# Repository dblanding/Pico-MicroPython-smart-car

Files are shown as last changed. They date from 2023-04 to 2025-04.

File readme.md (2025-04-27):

# Pico-&mu;Python Smart Car Project

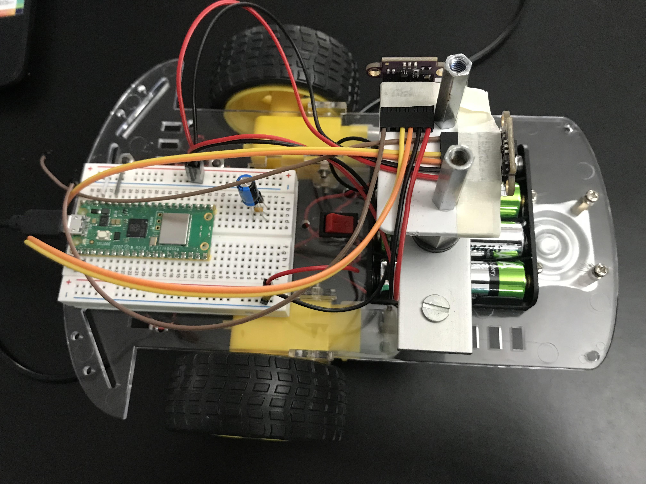
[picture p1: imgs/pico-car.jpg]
pico car


### This Medium article by Dan McCreary [Raspberry Pi Pico Robot in Micropython](https://dmccreary.medium.com/raspberry-pi-pico-robot-in-micropython-51f956486270) inspired me to buiild a similar smart car project
* Further details are presented at [base robot kit project](https://dmccreary.github.io/stem-robots/)
    * Discovered they use [MkDocs](https://www.mkdocs.org/getting-started/). May want to check this out sometime...

### My project will use **at least 2** of these time-of-flight VCSEL sensors

* Googled for info about Using the Raspberry Pi Pico with 2 x VL53L0x in Micropython
    * Found this [Orionrobots video](https://www.youtube.com/watch?v=XQrxPcq2tZ8) which shows:
        * Using two devices, one on each I2C bus
        * How to modify device address in order to have multiple devices on the same bus
        * in both cases, it is important to hold the XSHUT pin high.
    * The library used by Orionrobots is based on Kevin McAleer's [Raspberry Pi Pico & VL53L0X for MicroPython](https://www.youtube.com/watch?v=YBu6GKnN4lk)
    * Unfortunately, The library used (by both Kevin McAleeer and the derivative Orionrobots) only produces values up to 500 mm.
        * Whereas the datasheet shows the VL53L0X should produce data up to 1200 mm.
        * The VL53L0X library (used by McCreary) produces values all the way to 1200 mm. 
            * A diff shows that the libraries used by McAleer (and Orionrobots) is actually a mofified version of the one used by McCreary.
* I thought I would try using the **disparity** of two forward-looking but obliquely oriented (pigeon-toed) sensors as a way to enable the cheap *smart-car* to steer toward a wall along a path that is perpendicular to the wall. This proved to be quite difficult.
    * Without motor encoders, it is very frustrating trying to control steering on differential drive configuration.
    * The motors have a large and varialble amount of static friction, causing the actual motor speed to be unknowable. 
    * Sometimes, the friction is so large, that a motor won't start to turn even with a PWM duty cycle of (40_000 / 65_536)
    * Decided to not pursue this approach any further.
* Instead, I decided to use the Bosch BNO08x IMU sensor in RVC mode to keep track of the car's yaw angle.
* I will use the VCSEL sensors just for distance measurement

### Use the Bosch BNO08x IMU sensor to keep track of the car's **yaw** angle

* I found this [MicroPython library](https://github.com/rdagger/micropython-bno08x-rvc/blob/master/bno08x_rvc.py) (based on this [CircuitPython library](https://github.com/adafruit/Adafruit_CircuitPython_BNO08x_RVC)) which enables access to the BNO08x IMU module (in RVC mode) over the UART serial bus.
* (Truth be known, I was having a bit of difficulty figuring out how to attach more than one device to the I2C bus, so I decided to just sidestep this issue and connect over UART.)
* This primer on [Raspberry Pi Pico Serial Communication Example(MicroPython)](https://electrocredible.com/raspberry-pi-pico-serial-uart-micropython/) provided the detailed understanding I needed to get it all working.

### Use the [L298N motor driver module](https://www.etechnophiles.com/l298n-motor-driver-pin-diagram/)
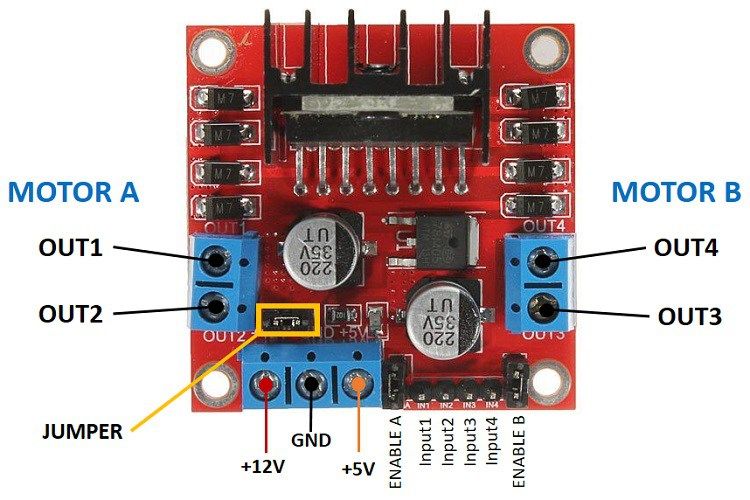
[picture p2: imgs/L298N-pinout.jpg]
L298N pinout

* Used on my ROS robot and it worked well, so I will use that again.

### Power to the pico will come from 2 different sources:
    1. The USB connection (5V)
    2. The 5V power output from the motor driver board
    
* The Pico datasheet shows a recommended way to accomodate power from 2 sources:

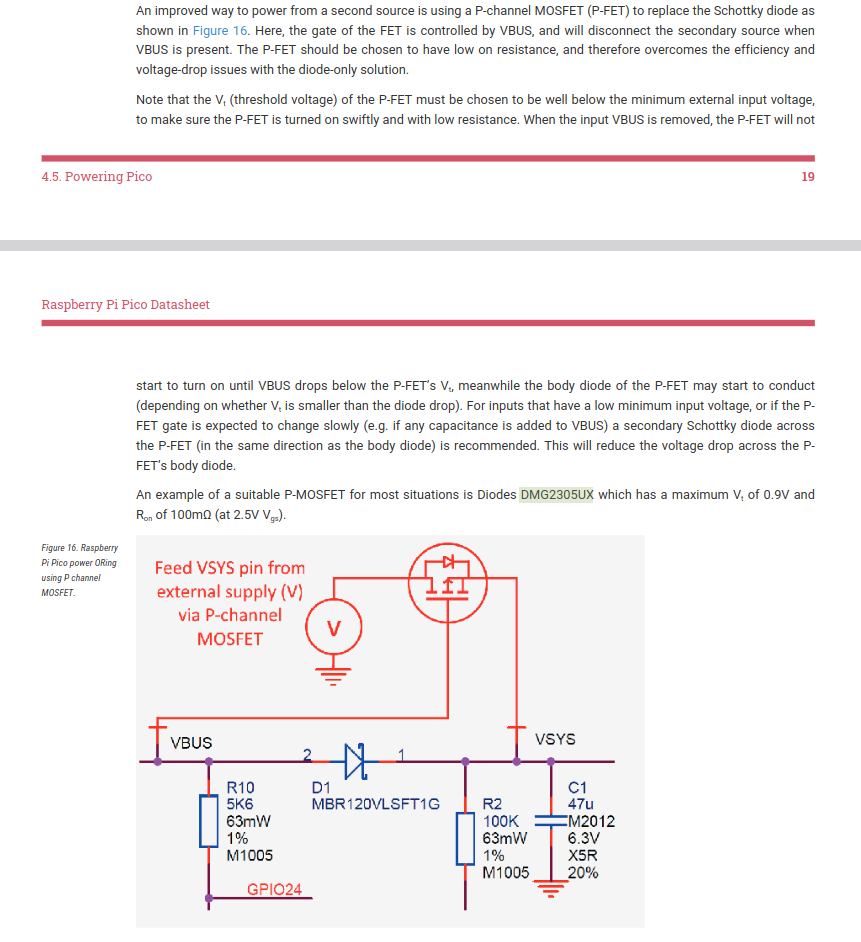
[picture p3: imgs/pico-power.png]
pico power


* I ordered the P-FET but until it comes, I have hooked up the 5V output from the motor driver board directly to the VSYS pin of the pico, as shown in this wiring diagram. It seems to work OK both with / without the USB connection to the Pico.

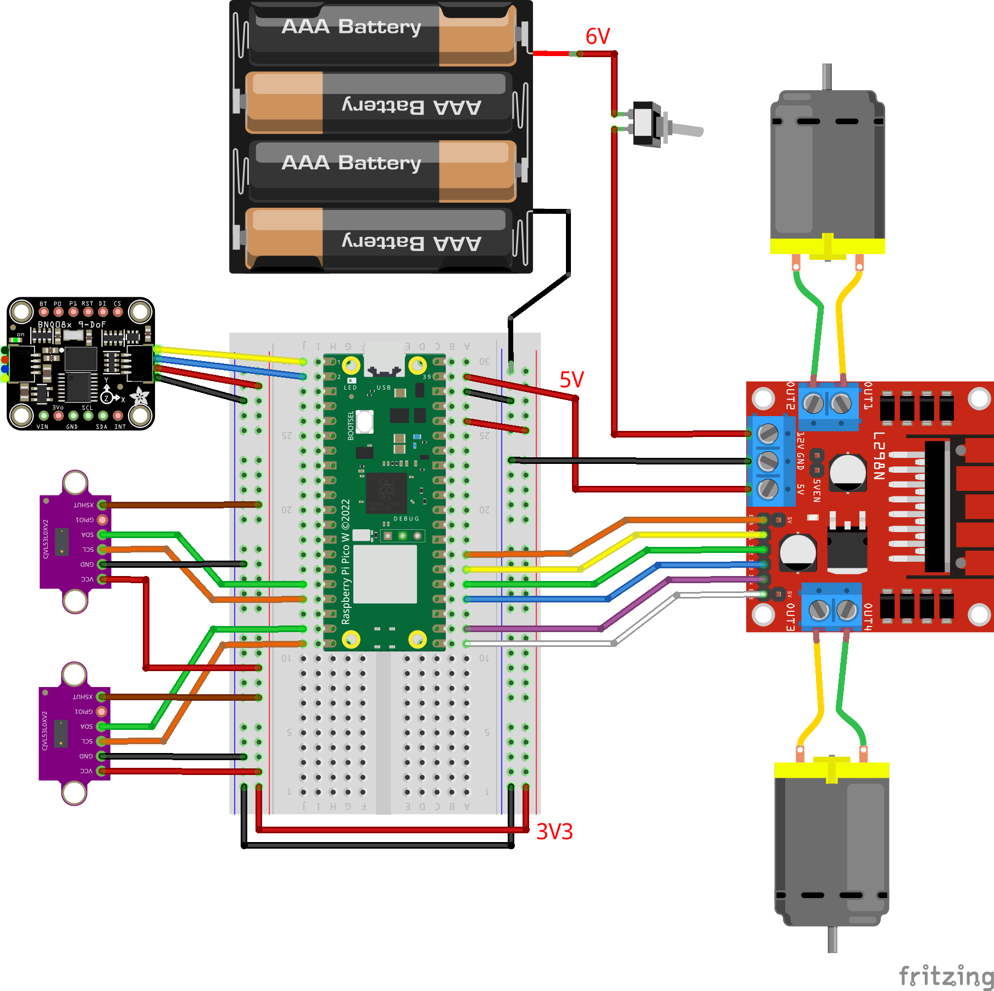
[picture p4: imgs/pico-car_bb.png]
Pico car wiring


* This video [Power for the Raspberry Pi Pico - Guide to using VBUS, VSYS and 3V3 for external power circuits](https://www.youtube.com/watch?v=3PH9jzRsb5E) reccomends using a Schotkey diode (1N5817) to allow connecting an external 5V supply to VSYS while the PICO is simultaneously connected to USB power.

### Add WiFi control

Bob Grant ([Bytes N Bits](https://bytesnbits.co.uk/S)) has produced this series of [3 video tutorials](https://www.youtube.com/playlist?list=PLvOT6zBnJyYGLmvrJeYzRYwBFa44SVnLZ) which teach how to build a web interface for controlling a project on the Pi Pico W.
* WiFi Control Your Micropython Project Using a Web Interface
    * [Youtube video](https://www.youtube.com/watch?v=eym8NpHr9Xw)
    * [Bytes N Bits web page](https://bytesnbits.co.uk/simple-micropython-wifi-connection/)
    * [Github Repo](https://github.com/getis/pi-pico-w-simple-wifi-setup)

* Web Control Panel Part 1: Add a web control panel to your project - the web server
    * [Youtube video](https://www.youtube.com/watch?v=h18LMskRNMA)
    * [Bytes N Bits web page](https://bytesnbits.co.uk/web-control-panel-web-server/)
    * [Github Repo](https://github.com/getis/micropython-web-control-panel)

* Web Control Panel Part 2: Asyncio & Dual Core web server
    * [Youtube video](https://www.youtube.com/watch?v=PY732g2ZN4g)
    * [Bytes N Bits web page](https://bytesnbits.co.uk/web-control-panel-2-asyncio-dual-core/)
    * [Github Repo](https://github.com/getis/micropython-web-control-panel)

* Web Control Panel Part 3: Web Page & Javascript coding
    * [Youtube video](https://www.youtube.com/watch?v=Z6g9x170Pvw)
    * [Bytes N Bits web page](https://bytesnbits.co.uk/web-control-panel-web-page/)
    * [Github Repo](https://github.com/getis/micropython-web-control-panel)

But first, just to get started, I will use a more primitive, basic web control interface.
Christopher Barnatt shows a very simple [Pi Pico W WiFi Controlled Robot](https://www.explainingcomputers.com/pi_pico_w_robot.html)
* The robot runs a basic webserver displaying a very simple form with 5 buttons.

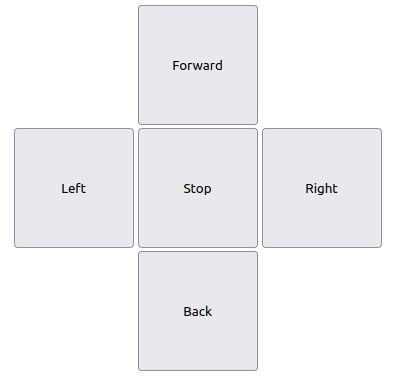
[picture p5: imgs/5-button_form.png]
webpage form


This looks just right for this project. Simple and straightforward. I just need the webserver to run asynchronously so it doesn't block the robot's navigation code.
* `pico_car+webserver.py` combines the web interface code the navigation code bundled together.

## Pause for project assessment

At this point, I have a nice, cheap mobile car platform for testing various robot-related concepts. And it is all running on the PICO-W.

Right now, if I set the car on the floor and turn it on, and then go to my laptop and browse to the car's webserver url (192.168.1.64), I get the car's 5-button navigtation panel.
* If I click the **Back** button, the car drives in reverse and it uses the PID feedback from the IMU to drive roughly straight in reverse (with some minor steering oscillations) until it arrives to within  250 mm of a wall.
* However if I click on the **Forward** button, the car goes forward, but drives as if it had a *steering wheel* that was turned 90 degrees to the left.
    * The left wheel was runnning slower than the right one.
    * Probably due to friction (I thought)
    * One possible cause was that the face of the left wheel hub was rubbing more against the motor housing, so I pried the wheel hubs away from the motor housing to create a small gap, but the problem persisted.
    * Whatever the cause of the difference in performance between the left and right motors, it is pointless to chase it down. There will always be differences.
    * Using yaw angle feedback from the IMU, I can get the car to drive straight in both the forward and reverse directions, but when turning in place, I won't know that both motors are turning (at the same speed).
        * For this reason, I decided that the motors must have encoders and the PID feedback from the encoders must be used to regulate the motor drive signals.
        * This of course, is the configuration of the ROS mobile robot, which makes further use of the encoder information to accurately compute odometry.

* Having come to the following realization, I decided to scrap the original chassis and motors, and begin again from scratch:

> The cute little yellow motors that come on the **DIY Smart Car** are altogether **inadequate** for use on a DIY robot. Any serious robot project must have motor shaft encoders and a gearbox with a reduction of at least 30 to 40x.

# Henceforth, this project is renamed **PicoBot**

* The original code is in the folder `code_other/`.
* The PicoBot code is in the folder `code_picobot/`.

## Find inexpensive gear motors with encoders for the Pico Car

I have been down this road previously and the best motors/wheels I found were the ones used by the Elegoo Tumbller. For the ROS robot, I wanted a higher gear reduction and ended up using motors with a 100:1 worm drive gear box.

For this project, I am not convinced that I need a different gear reduction, so I will proceed with the motors/wheels used by the Tumbller. I found them available for $12 apiece on [Aliexpress](https://www.aliexpress.us/item/2251832832394397.html?gatewayAdapt=glo2usa4itemAdapt) and [ordered 2](aliexpress-order/aliexpress-order.pdf).  There is a chart that shows various gearabox options. The Tumbller motor has a 30:1 gearbox with a length of 22 mm. Higher gear reductions can be gotten but have a greater length.  When I was looking for higher reduction motors for the ROS robot, I hadn't found these motors from Aliexpress. Looking at the Tumbller, it looks like there is enough room for the 24 mm length gearbox. So I could choose either 56:1 or 90:1 gear reductions.

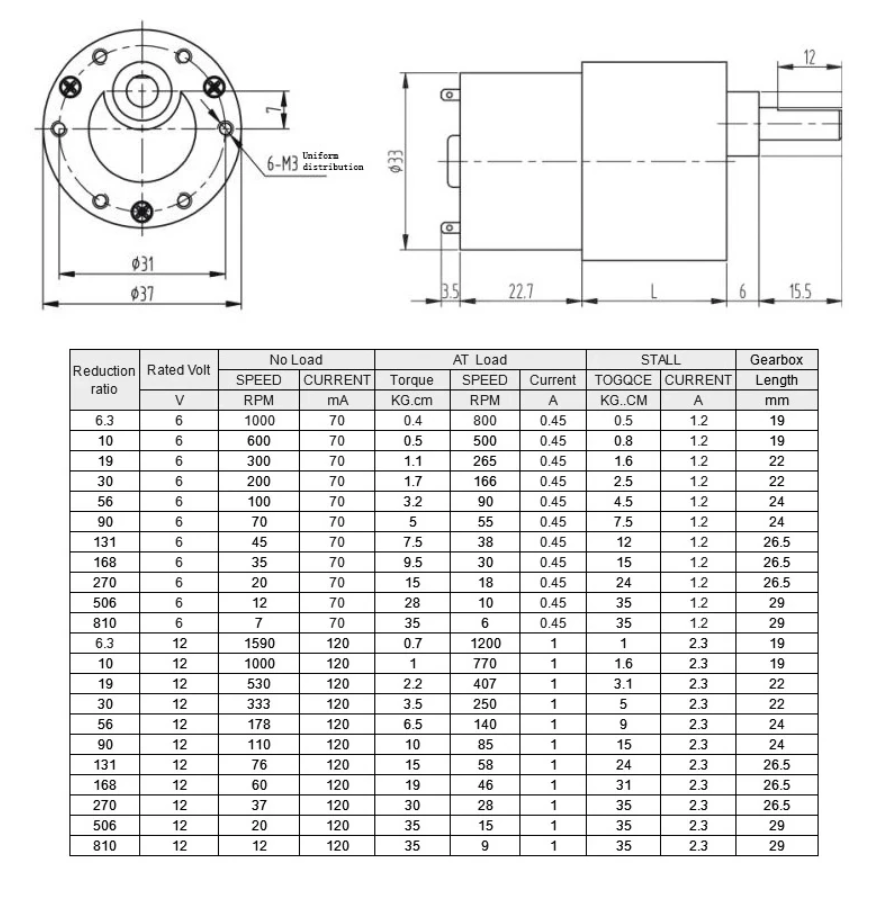
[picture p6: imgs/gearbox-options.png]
Gearbox Options


The motors come with a 6-wire harness which needs to be hooked up as follows:

- Red Wire - positive power supply of motor(+)(change positive and negative of motor the rotation will change)
- White Wire - negative power supply of motor(-)(change positive and negative of motor the rotation will change))
- Yellow Wire - signal feedback (motor one turn has 11 signals)
- Green Wire - signal feedback (motor one turn has 11 signals)
- Blue Wire - positive of encoder power supply(+)(3.3-5V),cannot be wrong
- Black Wire - negative of encoder power supply(-)(3.3-5V),cannot be wrong

## Program PICO to listen to encoder pulses on interrupts

Using the method shown in this video [Using PICO interrupts](https://www.youtube.com/watch?v=9Fio0BlMsVM), Chris DeHut shows how to set up the PICO to listen to encoder pulses.

* In the video, he has a link to the [code](https://makingstuffwithchrisdehut.com/electronics-files) which looks like an absolute gold mine of useful code for the PICO.

* For example, there are files there named: "encoders" and "analog joystick".
Those look like they would be worth looking at...

I found a collection of [Awesome MicroPython](https://awesome-micropython.com/#rotary-encoder) libraries which contains an encoder primer by Peter Hinch at this [repo](https://github.com/peterhinch/micropython-samples/blob/master/encoders/ENCODERS.md)
* He has written an [encoder library specifically for the Pico](https://github.com/peterhinch/micropython-samples/blob/master/encoders/encoder_rp2.py)
    * It uses some PIO and State Machine code (over my head) but seems to work very well, so I decided to use it. 
        * It counts **52 pulses per rev** which is likely counting both rising and falling edges of both sensors. (13 poles x 4)
        * This differs from the *"11 signals per rev"* quoted by the spec sheet (above).

## Pause again to evaluate project progress

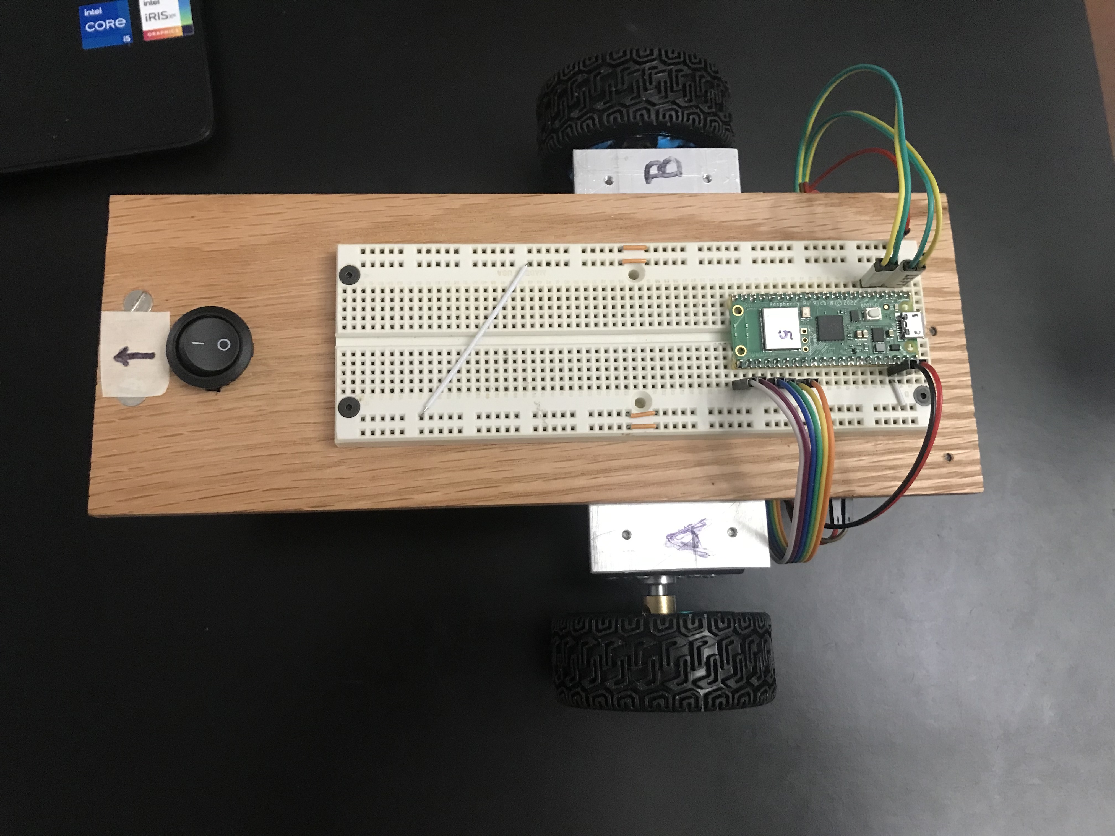
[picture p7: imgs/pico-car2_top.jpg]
Pico Car 2 (top)

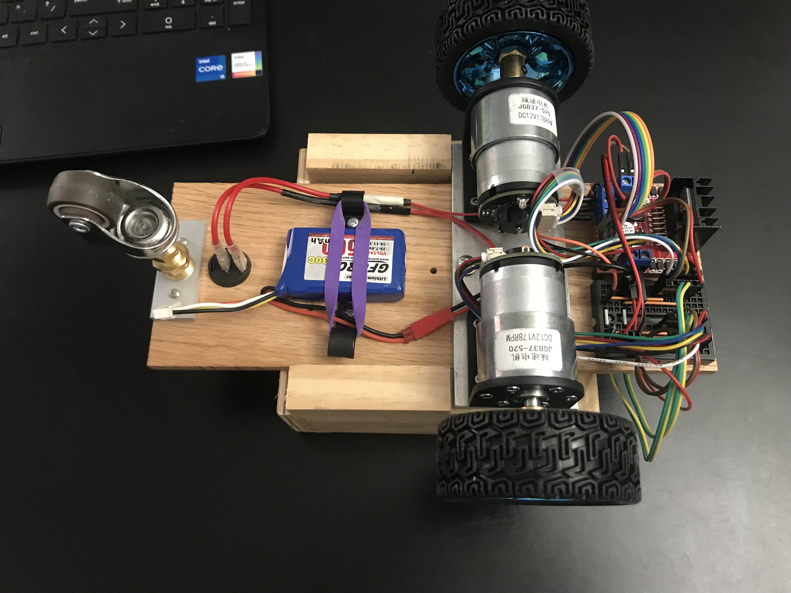
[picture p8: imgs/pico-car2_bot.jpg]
Pico Car 2 (bot)


* The car has been completely rebuilt to replace the little yellow smart car motors with the Tumbller motors. However, the new motors still have intrinsic differences that cause the car to turn excessively when intending to drive straight with the application of equal PWM signals.
* I replaced the 4-pack of AA batteries with a LiPo 3S 50C battery. This was to remedy the problem that as the AA batteries got a little tired, the 5V PS on the L298N was unable to provide 5V out and therefore was unable to power the Pico.
    * This solved the problem with the L293N P/S, but now the motors run much **faster** than they need to, so in order to operate at a moderate speed, a lower PWM signal is needed.

* I have received and installed the motors I ordered from AliExpress. (3 weeks from order to arrival)
    * It turns out they are the 56:1 motors.
    * This gear reduction works very well.
        * The cruising speed of the car is fine with the LiPo battery 
        * In-place turning works great with lower PWM values.
        * Decided to order another pair (spares)
    * For now, I drive the motors at a target tick rate of 4000 ticks/sec by applying an individual multiplier for each motor to arrive at a PWM signal that runs them both at approximately the same speed.
        * The PWM signals are in the vicinity of 50_000 (max value = 65,535)

* I am still using the 5-button web interface (asynchrouous) to control the car. This works OK, but it is pretty bare bones. I might want to explore a joystick for speed and direction control.
* I removed the VCSEL sensors and the IMU (for now) while I focus on getting the motors to use PID feedback from the encoders to drive at a target tick rate.

## Implement closed loop feedback motor speed control

* Wheel diameter = 2.682 inches (68.12 mm)
* Use encoder pulses in proportional feedback loop to control speed while driving forward and backward
* Using `encoder_test.py`, I found 2464 ticks for each revolution of the wheel.

| Factor | Source |
| ---- | ---- |
| 56 x | gear reduction |
| 11 x | magnetic poles on rotor |
|  4 x | detecting both rising and falling edges from 2 (quadrature) sensors |
| 2464 | Total (ticks per wheel rev) |

| Value | Parameter |
| ---- | ---- |
| 0.214 | Wheel circumference (meters) |
| 11_514 | ticks per meter |

* Even after optimizinging PID coefficients, there is still some visually detectable *wiggle* in the car's steering as it begins driving straight forward or backward.
    * Small differences in friction between the 2 motors cause them to come up to speed differently even under the control of the feedback loop.
    * To reduce this steering wiggle, I will try adding a 4th term (C) to the controller, minimizing the difference between the encoder counts of the two motors.
    * Adding a 'C' term makes the PID controller into a PIDC controller.
    * The C term keeps track of the cumulative tick counts for both motors, urging them to stay in lock step.
* To implement this, a single instance of the new motors.Motors class replaces the 2 instances of motor.Motor class. 
    * P (proportional)
    * I (integral)
    * D (Derivative)
    * C (count difference a / b)
* Got this working in both Forward & Back directions.
    * The steering wiggle is no longer visually noticeable.
    * Performance data of some 1 meter runs (FWD & BACK) are shown in [spreadsheets folder](spreadsheets).

## Other refinements

* Added Odometer class, which updates pose each time through the main loop.
    * `pose = Odometer.update(enc_a.value(), enc_b.value())`
    * `pose_x, pose_y, pose_angle = pose`
* Using pose_angle, left and right buttons can now turn to a goal_angle.
* Using encoder_values, driving forward and back can go to a goal_distance.

## Implemented Programmed Driving Instructions

* The main loop now loads the `instrux` list containing a sequence of `(drive_mode, goal)` tuples and executes them one-by-one.
* For example, here are the instructions to drive a 0.5 meter square in the CCW direction:
```
instrux = [('F', 0.5),
           ('L', pi / 2),
           ('F', 0.5),
           ('L', pi),
           ('F', 0.5),
           ('L', 3 * pi / 2),
           ('F', 0.5),
           ('L', 2 * pi)]
```

* After completing the sequence, the PicoBot continues to respond to web requests.

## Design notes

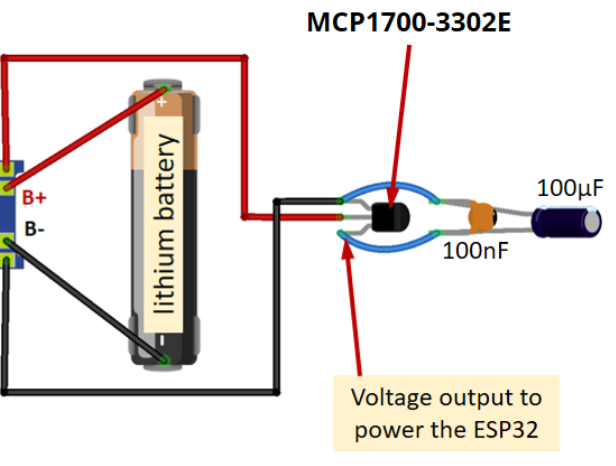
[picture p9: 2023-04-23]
imgs/mcp1700-3302e.png

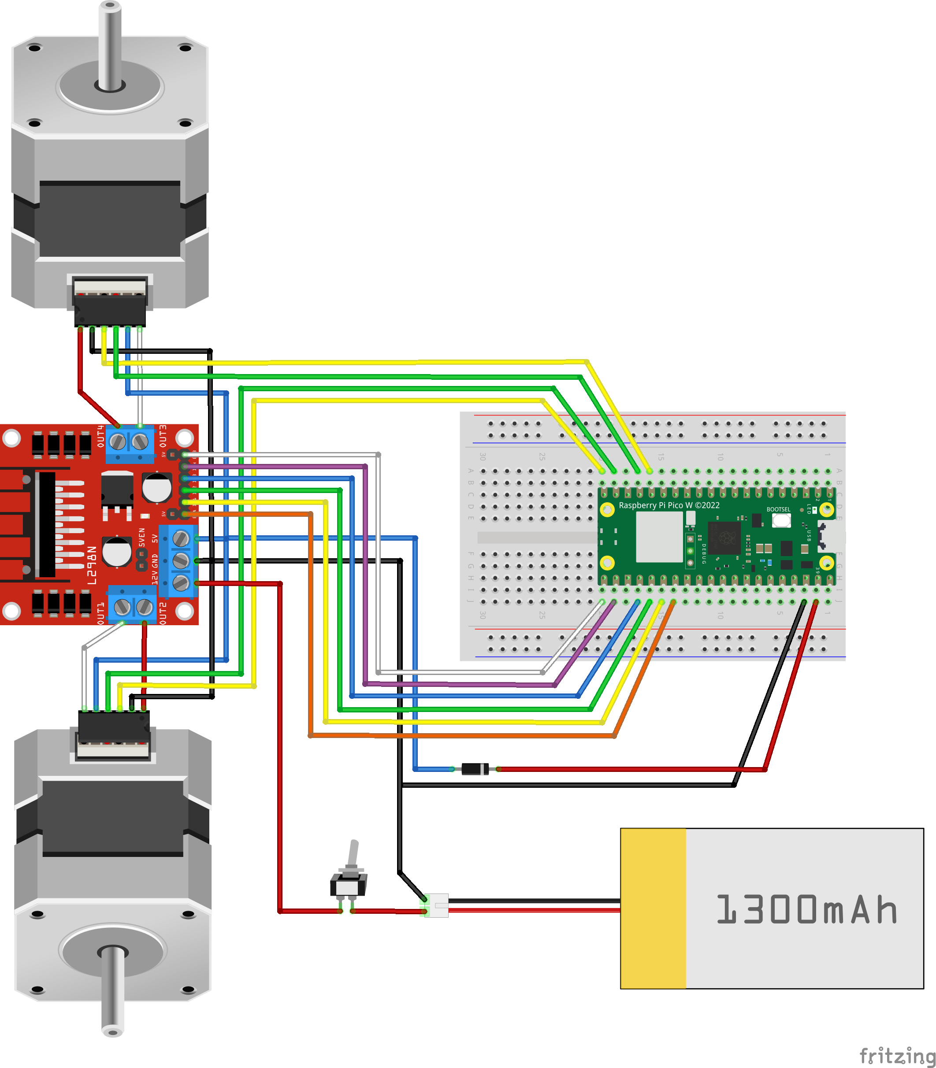
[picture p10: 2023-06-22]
imgs/pico-car2_bb.png

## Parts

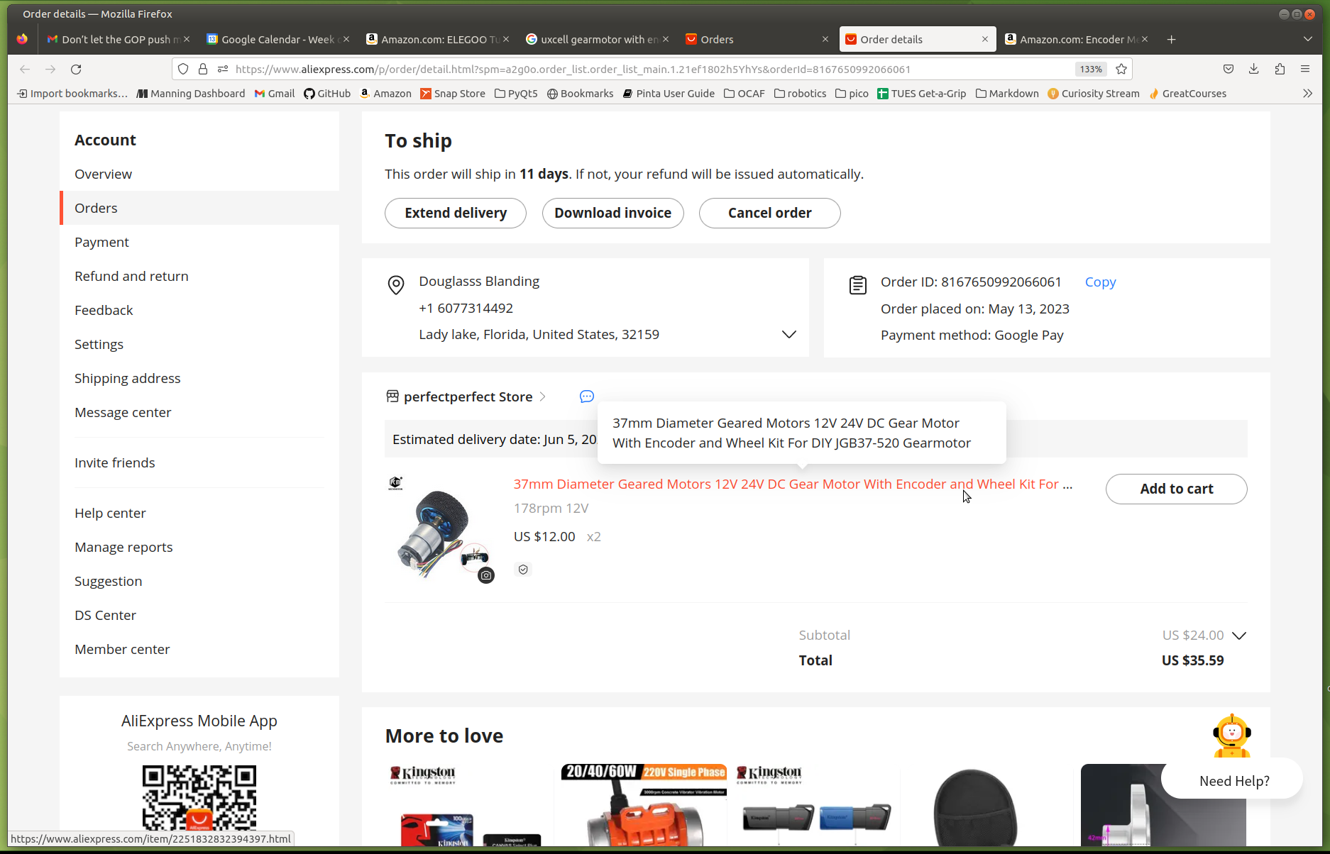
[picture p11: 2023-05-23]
aliexpress-order/aliexpress-order.png

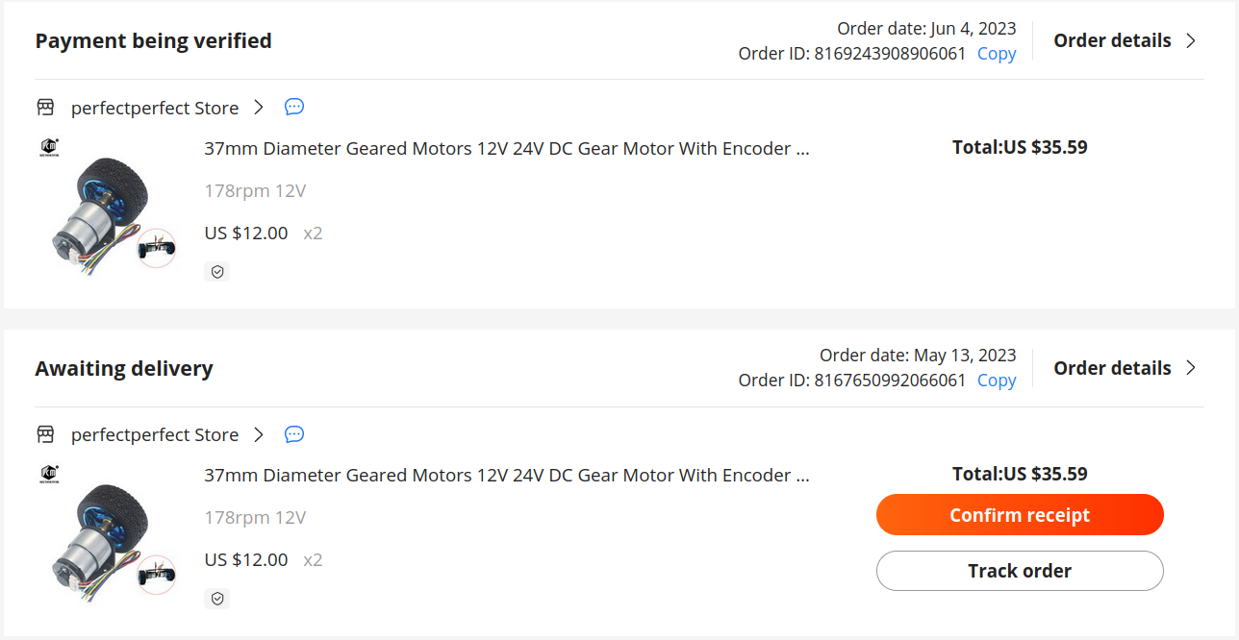
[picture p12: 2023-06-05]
aliexpress-order/Aliexpress-order2023-06-04.png

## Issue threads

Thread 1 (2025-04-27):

New Link for STEM Robots

dmccreary, 2025-04-27:
Hi Doug,

Thanks for referencing our site.

We are no longer working with CoderDojoTC or CodeSavvy

The new site is here:

https://dmccreary.github.io/stem-robots/

We would appreciate it if you would update the links.

Thanks! - Dan

dblanding, 2025-04-27:
Done

On Sun, Apr 27, 2025 at 1:14 PM Dan McCreary ***@***.***>
wrote:

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

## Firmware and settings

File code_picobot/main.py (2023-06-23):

"""
MicroPython code for Pico car project using:
* Raspberry Pi Pico mounted on differential drive car
* 56:1 gear motors with encoders
* Asynchrounous webserver enabling remote control
* Encoder feedback used in fwd and back modes to
    * drive motors at TARGET_TICK_RATE
    * PID (+C ) keeps wheels at target spd and
      in lock step despite motor differences
* Odometer keeps track of pose (x, y, angle)
* Follows list of driving instrux (drive_mode, goal)
* After completing instrux, drives in remote control mode
"""

import encoder_rp2 as encoder
import gc
import math
import network
import uasyncio as asyncio
import _thread
from machine import Pin, PWM
import time
from secrets import secrets
from motors import Motors
from odometer import Odometer
from parameters import TICKS_PER_METER, TARGET_TICK_RATE, TURN_SPD, ANGLE_TOL
from drive_instrux import instrux

ssid = secrets['ssid']
password = secrets['wifi_password']

# Set drive_mode to one of: 'F', 'B', 'R', 'L', 'S'
drive_mode = 'S'  # stop
goal = None

html = """<!DOCTYPE html>
<html>
    <head>
        <title>Robot Control</title>
    </head>

    <body>
        <center><b>

        <form action="./forward">
            <input type="submit" value="Forward" style="height:120px; width:120px" />
        </form>

        <table>
            <tr>
                <td><form action="./left">
                <input type="submit" value="Left" style="height:120px; width:120px" />
                </form></td>

                <td><form action="./stop">
                <input type="submit" value="Stop" style="height:120px; width:120px" />
                </form></td>

                <td><form action="./right">
                <input type="submit" value="Right" style="height:120px; width:120px" />
                </form></td>
            </tr>
        </table>

        <form action="./back">
        <input type="submit" value="Back" style="height:120px; width:120px" />
        </form>

    </body>
</html>
"""

# setup encoders
enc_b = encoder.Encoder(0, Pin(14))
enc_a = encoder.Encoder(1, Pin(12))

# setup onboard LED
led = Pin("LED", Pin.OUT, value=0)

# setup pins connected to L298N Motor Drive Controller Board
ena = PWM(Pin(21))
in1 = Pin(20, Pin.OUT, value=0)
in2 = Pin(19, Pin.OUT, value=0)
in3 = Pin(18, Pin.OUT, value=0)
in4 = Pin(17, Pin.OUT, value=0)
enb = PWM(Pin(16))

ena.freq(1_000)
enb.freq(1_000)

def set_mtr_dirs(a_mode, b_mode):
    """Set motor direction pins for both motors.
    options are: 'FWD', 'REV', 'OFF'."""

    if a_mode == 'FWD':
        in1.value(0)
        in2.value(1)
    elif a_mode == 'REV':
        in1.value(1)
        in2.value(0)
    else:  # Parked
        in1.value(0)
        in2.value(0)

    if b_mode == 'FWD':
        in3.value(0)
        in4.value(1)
    elif b_mode == 'REV':
        in3.value(1)
        in4.value(0)
    else:  # Parked
        in3.value(0)
        in4.value(0)

def set_mtr_spds(a_PWM_val, b_PWM_val):
    """set speeds for both a and b motors
    allowable values are u16 integers (< 65_536)"""

    ena.duty_u16(int(a_PWM_val))
    enb.duty_u16(int(b_PWM_val))

def move_forward():
    set_mtr_dirs('FWD', 'FWD')

def move_backward():
    set_mtr_dirs('REV', 'REV')

def turn_left():
    set_mtr_dirs('REV', 'FWD')

def turn_right():
    set_mtr_dirs('FWD', 'REV')

def move_stop():
    set_mtr_dirs('OFF', 'OFF')
    set_mtr_spds(0, 0)

# Stop the robot NOW
move_stop()

wlan = network.WLAN(network.STA_IF)

def connect():
    wlan.active(True)
    wlan.config(pm = 0xa11140) # Disable power-save mode
    wlan.connect(ssid, password)

    max_wait = 10
    while max_wait > 0:
        if wlan.status() < 0 or wlan.status() >= 3:
            break
        max_wait -= 1
        print('waiting for connection...')
        time.sleep(1)

    if wlan.status() != 3:
        raise RuntimeError('network connection failed')
    else:
        print('connected')
        status = wlan.ifconfig()
        ip = status[0]
        print('ip = ' + status[0])
    return ip

async def serve_client(reader, writer):
    global drive_mode, goal
    # print("Client connected")
    request_line = await reader.readline()
    request_line = str(request_line)
    # print("Request:", request_line)
    # We are not interested in HTTP request headers, skip them
    while await reader.readline() != b"\r\n":
        pass

    try:
        command = request_line.split()[1]
    except IndexError:
        pass
    print("command = ", command)
    if command == '/forward?':
        drive_mode  = 'F'
        goal = 1
    elif command =='/left?':
        drive_mode = 'L'
        goal = None
    elif command =='/stop?':
        drive_mode = 'S'
    elif command =='/right?':
        drive_mode = 'R'
        goal = None
    elif command =='/back?':
        drive_mode = 'B'
        goal = 1

    response = html
    writer.write('HTTP/1.0 200 OK\r\nContent-type: text/html\r\n\r\n')
    writer.write(response)

    await writer.drain()
    await writer.wait_closed()
    # print("Client disconnected")

async def main():
    global drive_mode, goal
    print('Connecting to Network...')
    connect()

    print('Setting up webserver...')
    asyncio.create_task(asyncio.start_server(serve_client, "0.0.0.0", 80))
    start_time = time.ticks_ms()
    prev_time = time.ticks_ms()
    prev_mode = 'S'  # stop
    odom = Odometer()
    while True:

        # Flash LED
        led.toggle()

        # get next driving instruction
        if drive_mode == 'S' and len(instrux):
            drive_mode, goal = instrux.pop(0)

        # get latest encoder values
        enc_a_val = enc_a.value()
        enc_b_val = enc_b.value()

        # get current pose
        pose = odom.update(enc_a_val, enc_b_val)
        pose_x, pose_y, pose_angle = pose
        pose_ang_deg = pose_angle * 180 / math.pi
        pose_deg = (pose_x, pose_y, pose_ang_deg)  # for display

        # Check to see if drive_mode has changed
        if drive_mode != prev_mode:
            prev_mode = drive_mode
            mtrs = None
            gc.collect()
            if drive_mode == 'F':
                # Instantiate Motors object
                mtrs = Motors(TARGET_TICK_RATE)
                
                # Set direction pins
                move_forward()
                
                # save starting value of encoders
                enc_a_start = enc_a.value()
                enc_b_start = enc_b.value()

            elif drive_mode == 'B':
                # Instantiate Motors object
                mtrs = Motors(TARGET_TICK_RATE, fwd=False)
                
                # Set direction pins
                move_backward()
                
                # save starting value of encoders
                enc_a_start = enc_a.value()
                enc_b_start = enc_b.value()

            elif drive_mode in ('L', 'R'):
                # set goal_angle (abs)
                goal_angle = goal

            elif drive_mode == 'S':
                # Stop motors
                move_stop()
                del(mtrs)

        # Drive forward to goal_distance
        if drive_mode == 'F':
            goal_distance = goal
            goal_a = enc_a_start + (goal_distance * TICKS_PER_METER)
            if enc_a.value() < goal_a:
                pwm_a, pwm_b = mtrs.update(enc_a.value(), enc_b.value())
                set_mtr_spds(pwm_a, pwm_b)
                # print(pose)
            else:
                drive_mode = 'S'
                move_stop()
                del(mtrs)

        # Drive backward to goal_distance
        if drive_mode == 'B':
            goal_distance = goal
            goal_a = enc_a_start - (goal_distance * TICKS_PER_METER)
            if enc_a.value() > goal_a:
                pwm_a, pwm_b = mtrs.update(enc_a.value(), enc_b.value())
                set_mtr_spds(pwm_a, pwm_b)
                # print(pose)
            else:
                drive_mode = 'S'
                move_stop()
                del(mtrs)

        # Turn to goal_angle
        if drive_mode in ('L', 'R') and goal_angle:
            if pose_angle < (goal_angle - ANGLE_TOL):
                turn_left()
                set_mtr_spds(TURN_SPD, TURN_SPD)
                print(pose_deg)
            elif pose_angle > (goal_angle + ANGLE_TOL):
                turn_right()
                set_mtr_spds(TURN_SPD, TURN_SPD)
                print(pose_deg)
            else:
                drive_mode = 'S'
                move_stop()
                print(pose_deg)

        # Turn left
        if drive_mode == 'L' and not goal:
            turn_left()
            set_mtr_spds(TURN_SPD, TURN_SPD)
            print(pose_deg)
            print('goal = ', goal)
            
        # Turn right
        if drive_mode == 'R' and not goal:
            turn_right()
            set_mtr_spds(TURN_SPD, TURN_SPD)
            print(pose_deg)
            print('goal = ', goal)

        await asyncio.sleep(0.1)

try:
    asyncio.run(main())
finally:
    asyncio.new_event_loop()

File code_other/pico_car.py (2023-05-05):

"""
MicroPython code for Pico car project using:
* Raspberry Pi Pico mounted on differential drive 'smart car'
* 2 VL53L0x time-of-flight distance sensors
    (keep XSHUT pin on VL53L0X devices pulled high)
* BNO08X IMU reports yaw angle
* Yaw angle feedback enables:
    - car to drive straight
    - make measured turns in place
"""

from machine import Pin, I2C, PWM, UART
import time
import VL53L0X
from bno08x_rvc import BNO08x_RVC

# setup IMU in RVC mode on UART
uart = UART(0, baudrate=115200, tx=Pin(0), rx=Pin(1))
print(uart)
rvc = BNO08x_RVC(uart)
yaw, r, p, x, y, z = rvc.heading

# setup onboard LED and turn it on
led = Pin("LED", Pin.OUT, value=1)

# pins connected to L298N Motor Drive Controller Board
ena = PWM(Pin(21))
in1 = Pin(20, Pin.OUT, value=0)
in2 = Pin(19, Pin.OUT, value=0)
in3 = Pin(18, Pin.OUT, value=0)
in4 = Pin(17, Pin.OUT, value=0)
enb = PWM(Pin(16))

ena.freq(1_000)
ena.freq(1_000)

def set_mtr_dirs(a_mode, b_mode):
    """Set motor direction pins for both motors.
    options are: 'FWD', 'REV', 'OFF'."""

    if a_mode == 'FWD':
        in1.value(0)
        in2.value(1)
    elif a_mode == 'REV':
        in1.value(1)
        in2.value(0)
    else:  # Parked
        in1.value(0)
        in2.value(0)

    if b_mode == 'FWD':
        in3.value(0)
        in4.value(1)
    elif b_mode == 'REV':
        in3.value(1)
        in4.value(0)
    else:  # Parked
        in3.value(0)
        in4.value(0)

def set_mtr_spds(a_PWM_val, b_PWM_val):
    """set speeds for both a and b motors
    allowable values are u16 integers (< 65_536)"""

    ena.duty_u16(a_PWM_val)
    enb.duty_u16(b_PWM_val)


def setup_tof_sensor(bus_id, sda_pin, scl_pin):
    """Setup a Vcsel sensor on an I2C bus.
    There are two available busses: 0 & 1.
    Return VL53L0X object."""
    sda = Pin(sda_pin)
    scl = Pin(scl_pin)

    print("setting up i2c%s" % bus_id)
    i2c = I2C(id=bus_id, sda=sda, scl=scl)
    print("Set up device %s on i2c%s" % (i2c.scan(), bus_id))

    return VL53L0X.VL53L0X(i2c)


tof0 = setup_tof_sensor(0, 12, 13)  # right sensor
tof1 = setup_tof_sensor(1, 14, 15)  # rear sensor
tof0.start()
tof1.start()

def go_back_to_wall(space):
    """Go until back sensor distance == space (mm)"""
    # Motor control parameters
    nom_spd = 45_000
    kp = 1500  # Proportional PID coefficient
    kd = 2500  # Derivative PID coefficient (dissipative)
    p_trim = 0
    d_trim = 0
    p_trim_limit = 10_000
    yaw_prev = 0

    try:
        d1 = tof1.read()
        set_mtr_dirs('REV', 'REV')
        set_mtr_spds(nom_spd, nom_spd)
        while  d1 > space:
            d1 = tof1.read()
            yaw, r, p, x, y, z = rvc.heading
            p_trim = int(yaw * kp)
            if p_trim > p_trim_limit:
                p_trim = p_trim_limit
            elif p_trim < -p_trim_limit:
                p_trim = -p_trim_limit
            d_trim = int( (yaw - yaw_prev) * kd)
            yaw_prev = yaw
            a_spd = nom_spd - p_trim - d_trim
            b_spd = nom_spd + p_trim + d_trim
            print(yaw, d1, a_spd, b_spd, p_trim, d_trim)
            set_mtr_spds(a_spd, b_spd)
            time.sleep(0.01)
        set_mtr_dirs('OFF', 'OFF')
        print('stop')
        
        # Print some values as car coasts to a complete stop
        for cycle in range(15):
            d1 = tof1.read()
            yaw, p, r, x, y, z = rvc.heading
            print(yaw, d1)
            time.sleep(0.01)
    finally:
        led.off()
        tof0.stop()
        tof1.stop()
        set_mtr_dirs('OFF', 'OFF')
        set_mtr_spds(0, 0)


if __name__ == "__main__":
    go_back_to_wall(250)

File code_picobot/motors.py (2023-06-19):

import time

class Motors():
    """
    Calculate and return PWM signals for both motors using encoder feedback
    in a PIDC controller:
        
    P - Proportional
    I - Integral
    D - Derivative
    C - Count difference (a/b)

    """

    def __init__(self, target_tick_rate, fwd=True, multiplier=11,
                 EKP=-0.002, EKI=-0.001, EKD=-0.05, EKC=-0.01):
        self.multiplier = multiplier
        self.ttr = target_tick_rate
        self.fwd = fwd
        self.rate_list_a = []
        self.rate_list_b = []
        # encoder control loop coefficients
        self.EKP = EKP  # proportional
        self.EKI = EKI  # integral
        self.EKD = EKD  # derivative
        self.EKC = EKC  # count difference
        self.initialized = False

    def update(self, curr_cnt_a, curr_cnt_b):
        """
        return (pwm_a, pwm_b)
        
        error = (actual tick rate - target tick rate)
        """

        if not self.initialized:
            # Initialize values on first update
            self.initialized = True
            self.start_cnt_a = curr_cnt_a
            self.prev_cnt_a = curr_cnt_a
            self.start_cnt_b = curr_cnt_b
            self.prev_cnt_b = curr_cnt_b
            self.prev_rate_a = 0
            self.prev_rate_b = 0
            self.prev_time = time.ticks_ms()
            self.start_time = time.ticks_ms()
            pwm_a = 0
            pwm_b = 0
            print('p_trim_a, i_trim_a, d_trim_a, c_trim_a')
            # print('total_cnt_a, total_cnt_b, rate_a, rate_b')
        else:
            # control motor speed on subsequent updates
            
            # calculate delta tick counts since previous update
            curr_time = time.ticks_ms()
            delta_time = curr_time - self.prev_time
            delta_cnt_a = curr_cnt_a - self.prev_cnt_a
            delta_cnt_b = curr_cnt_b - self.prev_cnt_b
            
            # Keep track of accumulated total counts
            total_cnt_a = curr_cnt_a - self.start_cnt_a
            total_cnt_b = curr_cnt_b - self.start_cnt_b
            
            # speed is always positive
            delta_cnt_a = abs(delta_cnt_a)
            delta_cnt_b = abs(delta_cnt_b)

            # calculate current tick rate (ticks per sec)
            self.prev_time = curr_time
            self.prev_cnt_a = curr_cnt_a
            self.prev_cnt_b = curr_cnt_b
            if delta_time == 0:
                # avoid dividing by zero
                rate_a = 0
                rate_b = 0
            else:
                # delta_time is in ms thus * 1_000 below
                rate_a = (delta_cnt_a / delta_time) * 1_000
                rate_b = (delta_cnt_b / delta_time) * 1_000

            # proportional
            # error = actual tick rate - target tick rate
            p_err_a = rate_a - self.ttr
            p_trim_a = p_err_a * self.EKP
            p_err_b = rate_b - self.ttr
            p_trim_b = p_err_b * self.EKP
            
            # integral
            i_err_a = self._accumulated(p_err_a, self.rate_list_a)
            i_trim_a = self.EKI * i_err_a
            i_err_b = self._accumulated(p_err_b, self.rate_list_b)
            i_trim_b = self.EKI * i_err_b


            # derivative
            if delta_time == 0:
                d_err_a = 0
                d_err_b = 0
            else:
                d_err_a = (rate_a - self.prev_rate_a) / delta_time
                d_err_b = (rate_b - self.prev_rate_b) / delta_time
                self.prev_rate_a = rate_a
                self.prev_rate_b = rate_b
            d_trim_a = d_err_a * self.EKD
            d_trim_b = d_err_b * self.EKD
            
            # yaw caused by total_cnt_a total_cnt_b difference
            cnt_err = total_cnt_a - total_cnt_b
            
            # need to reverse for driving backwards
            if not self.fwd:
                cnt_err = -cnt_err
            
            c_trim_a = cnt_err * self.EKC
            c_trim_b = -cnt_err * self.EKC

            print(p_trim_a, i_trim_a, d_trim_a, c_trim_a)
            # print(total_cnt_a, total_cnt_b, rate_a, rate_b)

            mult_a = self.multiplier + p_trim_a + i_trim_a + d_trim_a + c_trim_a
            mult_b = self.multiplier + p_trim_b + i_trim_b + d_trim_b + c_trim_b

            # calculate PWM values
            pwm_a = int(self.ttr * (mult_a))
            pwm_b = int(self.ttr * (mult_b))
            if pwm_a > 65_530:
                pwm_a = 65_530
            if pwm_b > 65_530:
                pwm_b = 65_530
            
        return pwm_a, pwm_b

    def _accumulated(self, rate, rate_list):
        """return sum of previous values of rate"""

        if len(rate_list) == 100:
            _ = rate_list.pop(0)
        rate_list.append(rate)
        return sum(rate_list)

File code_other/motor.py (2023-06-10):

import time

class Motor():
    """
    Calculate and return PWM signal (uint 16) to acieve:
    1. Brief open loop operation while motor comes up to speed
    2. Closed loop operation using encoder feedback
        to maintain actual tick rate == target tick rate
    """

    def __init__(self, target_rate, multiplier, KP=-0.001, KD=1.2, KI=0):
        self.multiplier = multiplier
        self.target_rate = target_rate
        self.KP = KP
        self.KI = KI
        self.KD = KD
        self.initialized = False

    def update(self, tick_cnt):
        """
        Return pwm value to drive motor
        
        error = (actual tick rate - target tick rate)
        """

        if not self.initialized:
            # Initialize values on first update
            self.initialized = True
            self.prev_cnt = tick_cnt
            self.prev_rate = 0
            self.prev_time = time.ticks_ms()
            self.start_time = time.ticks_ms()
            self.rate_list = []
            pwm_val = 0
            print('rate Multiplier p_trim d_trim')
        else:
            # Calculate PWM value
            if (time.ticks_ms() - self.start_time) < 600:
                # Disable PID feedback while motor comes up to speed
                pwm_val = self.target_rate * self.multiplier
            else:
                # Enable PID feedback loop
                curr_time = time.ticks_ms()
                elapsed_time = curr_time - self.start_time
                delta_time = curr_time - self.prev_time
                delta_cnt = tick_cnt - self.prev_cnt
                
                # If driving backwards, speed is still positive
                delta_cnt = abs(delta_cnt)

                self.prev_time = curr_time
                self.prev_cnt = tick_cnt
                if delta_time == 0:
                    rate = 0
                else:
                    rate = (delta_cnt / delta_time) * 1_000
                proportional_error = rate - self.target_rate
                p_trim = self.KP * proportional_error

                if delta_time == 0:
                    derivative_error = 0
                else:
                    derivative_error = (rate - self.prev_rate) / delta_time
                    self.prev_rate = rate
                d_trim = self.KD * derivative_error

                integral_error = self._accumulated(proportional_error)
                i_trim = self.KI * integral_error

                self.multiplier += p_trim

                nominal = self.target_rate * self.multiplier
                pwm_val = int(nominal + p_trim + i_trim + d_trim)
                print(rate, self.multiplier, p_trim, d_trim)
                if pwm_val > 65_530:
                    pwm_val = 65_530

        return pwm_val

    def _accumulated(self, rate):
        """return sum of last 10 values of rate"""

        if len(self.rate_list) == 10:
            _ = self.rate_list.pop(0)
        self.rate_list.append(rate)
        return sum(self.rate_list)

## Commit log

2023-04-23 inital commit
    [pico-car.fzz]
2023-04-24 Added IMU to fritzing diagram, Added g0_until_wall function with improved PID
    [pico-car.fzz]
2023-05-23 replaced 'smart-car' motors with 'Tumbller' motors replaced AA batteries with LiPo 3S battery
    [encoder_rp2.py, move_fwd_foo.py]
2023-06-03 30:1 gear motors replaced with 56:1 motors
    [bt_foo.py]
2023-06-05 revised motor.Motor to adjust multiplier
2023-06-06 PID speed control for driving forward and back
2023-06-07 stable operation driving with 5-button web interface
2023-06-08 Tweaked PID coefficients
2023-06-09 Added BNO08x IMU on default UART pins 0 & 1. Moved encoder pins to 16-20.
2023-06-09 changed loop delay from 0.1 to 0.01 sec to benefit IMU data
2023-06-10 Added motors.Motors class, combining individual Motor objects into one. This enables adding a count_differernce (C) term to the feedback controller to keep the two motors in lock step (more or less).
2023-06-11 PIDC controller working in FWD & BACK modes
    [fwd-back-no-c_term.ods, fwd-back-yes-c_term.ods]
2023-06-12 Cleaned up to remove vestiges of IMU code which isn't being used.
2023-06-22 Reorganized code into 2 folders, current code in code_picobot2
    [pico-car2.fzz]
